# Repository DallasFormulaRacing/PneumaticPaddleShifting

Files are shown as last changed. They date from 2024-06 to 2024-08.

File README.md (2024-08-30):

# PneumaticPaddleShifting

## Table of Contents
1. [Objective](#objective)
2. [Hardware and Equipment](#hardware-and-equipment)
3. [Firmware Tech Stack](#firmware-tech-stack)
4. [Automation](#automation)
5. [Design](#design)

## Objective:
- Optimize the user's response to a down-shift and up-shift command.
- Maintain strict practices and edge cases for critical safety.
- Build the first fully-fledged DAQ with re-usable code through:
    - The Layered Architecture design pattern
    - Modularity of components
    - Hardware abstraction

## Hardware and Equipment
### Target Device
The [STM32 Nucleo F466RE](https://www.st.com/en/evaluation-tools/nucleo-f446re.html) microcontroller development board is used as the current target device for code merged to the `main` and `develop` branches. Theoretically, other Arm Cortex M4 based STM32 devices with the necessary peripherals should be able to run the same program.



## Firmware Tech Stack
- STM32 Hardware Abstraction Layer ([HAL](https://www.st.com/resource/en/user_manual/um1725-description-of-stm32f4-hal-and-lowlayer-drivers-stmicroelectronics.pdf))
  - Generated by STM32CubeMX within the CubeIDE environment, which also provides the `arm-none-eabi` toolchain.
  - Serves as a set of drivers or a Board Support Package (BSP) to interface with the microcontroller.

## Automation
- Unit tests are developed using [Google Test](https://google.github.io/googletest/) and are maintained in `Shifter_System/Tests`.
- See our [Unit Testing page](https://github.com/DallasFormulaRacing/DataAcquisition2.0/wiki/Unit-Testing) for running them locally by leveraging [Docker](https://docs.docker.com/get-started/overview/).
- Continuous Integration (CI)
  - The firmware is compiled as an stm32CubeIDE project using the following GitHub Action: [xanderhendriks/action-build-stm32cubeide](https://github.com/marketplace/actions/build-stm32cubeide-project).
  - The unit tests are compiled and ran using [CMake](https://cmake.org/cmake/help/latest/index.html) with [Ninja](https://ninja-build.org/manual.html). 

## Design

High level system diagram:

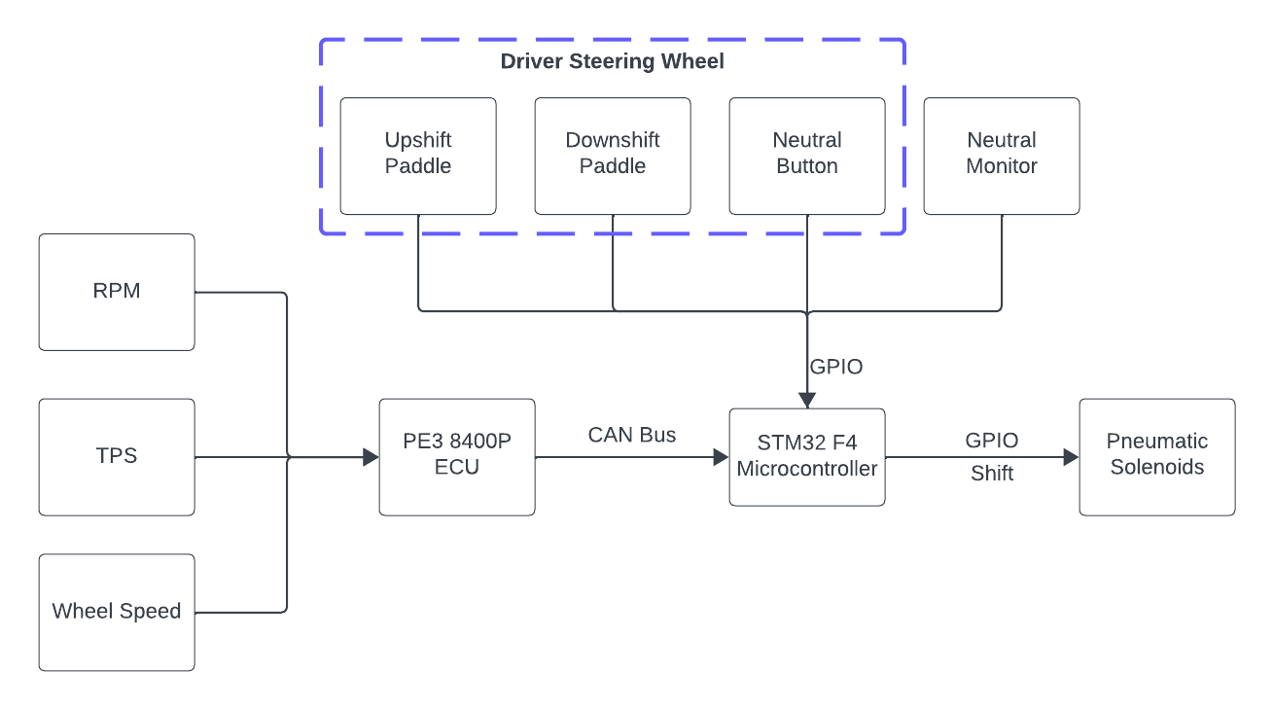
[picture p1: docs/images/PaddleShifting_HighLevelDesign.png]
High Level System Diagram


Firmware design:

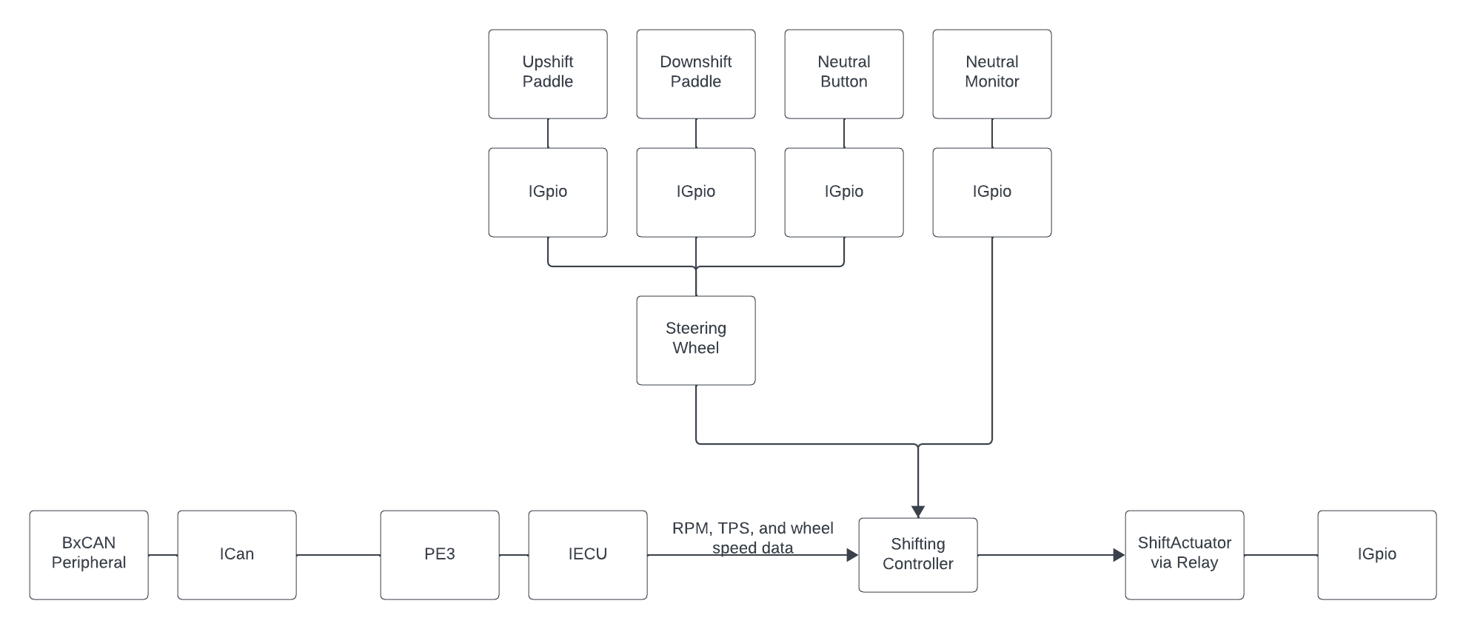
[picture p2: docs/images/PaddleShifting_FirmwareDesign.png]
Firmware Design


### User Input

It is assumed that the user inputs are simple GPIO signals (i.e., high and low voltages). The upshift and downshift paddle will request their respective shift. The neutral button is for the user to set the car into neutral, and this may be verified with a neutral “monitor”. The neutral monitor is to act as some sort of sensor or switch.  

Do note, however, that these inputs have not yet been tested. It is currently unknown whether they will require any signal “debouncing” so that the behavior is not jittery or sporadic. It has also been highly recommended to consider more fail-safe mechanisms for the scenario that the user input begins to malfunction. 

### Reading ECU Data

The device reads RPM, TPS, and wheel speeds from the PE3 8400-P ECU. This ECU implementation library was adopted from the race team’s previous efforts in other projects. 

### Shift Controller

The Shift Controller is a high-level component responsible for evaluating the driver’s shift requests. It depends on an ECU and several GPIO components to be used. Internally, a state machine is used to perform different behaviors. This approach offers the following advantages: dramatically simplifies the logic, increases performance, isolated behavior, and transition actions. The performance is increased as it only performs the conditional checks that are unique to each state. Due to the isolated behaviors, we can also easily determine and rigorously test every edge case for every state.

You may see the design of the state machine below in Figure 9. In practice, there are 6 gears. However, gears 2 through 5 had the same logic and state transition conditions, so they were condensed into a single state. So, the nomenclature was established as the following: Low Gear refers to first gear, Mid Gears refers to second to fifth gear, and High Gear refers to sixth gear. 

One important design choice is how we intended to manage the transition to/from the neutral state. In practice, to go from first to second gear, the driver typically needs to go through neutral. Although an “immediate pass-through" transition was considered, the team ultimately decided to require the driver to manually transition through neutral. This user experience will be in reminiscence of a typical vehicle to offer a more seamless and practical learning curve to use. 

It is worth mentioning that, due to time constraints in the development of the Shift Actuation, the Shift Controller is incomplete in respect to commanding for a shift. 

`ShiftController` state machine:

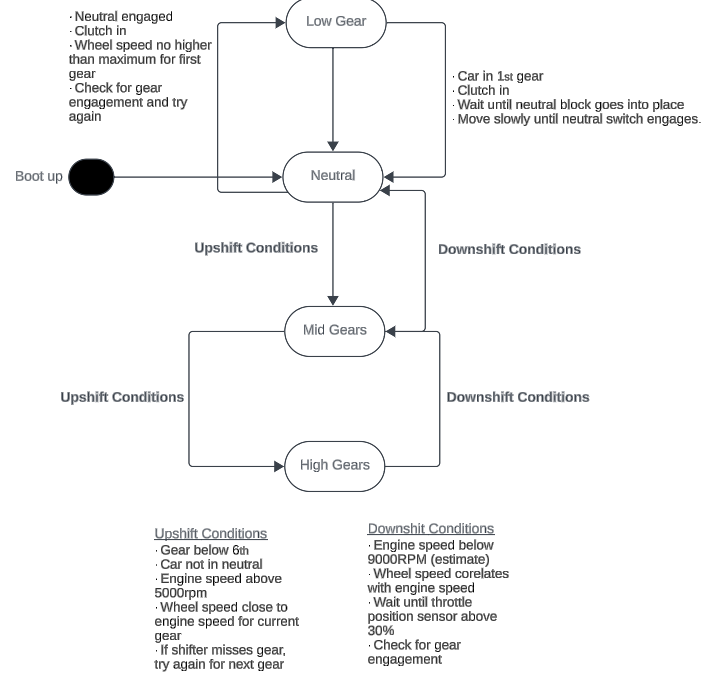
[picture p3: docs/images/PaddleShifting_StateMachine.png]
Shift Controller State Machine


### Shift Actuation

It is assumed that the required hardware interface for the shift actuator would be a GPIO (i.e., high and low) signal. However, due to time constraints, requirements of the hardware interface were not tested and verified for modifications.

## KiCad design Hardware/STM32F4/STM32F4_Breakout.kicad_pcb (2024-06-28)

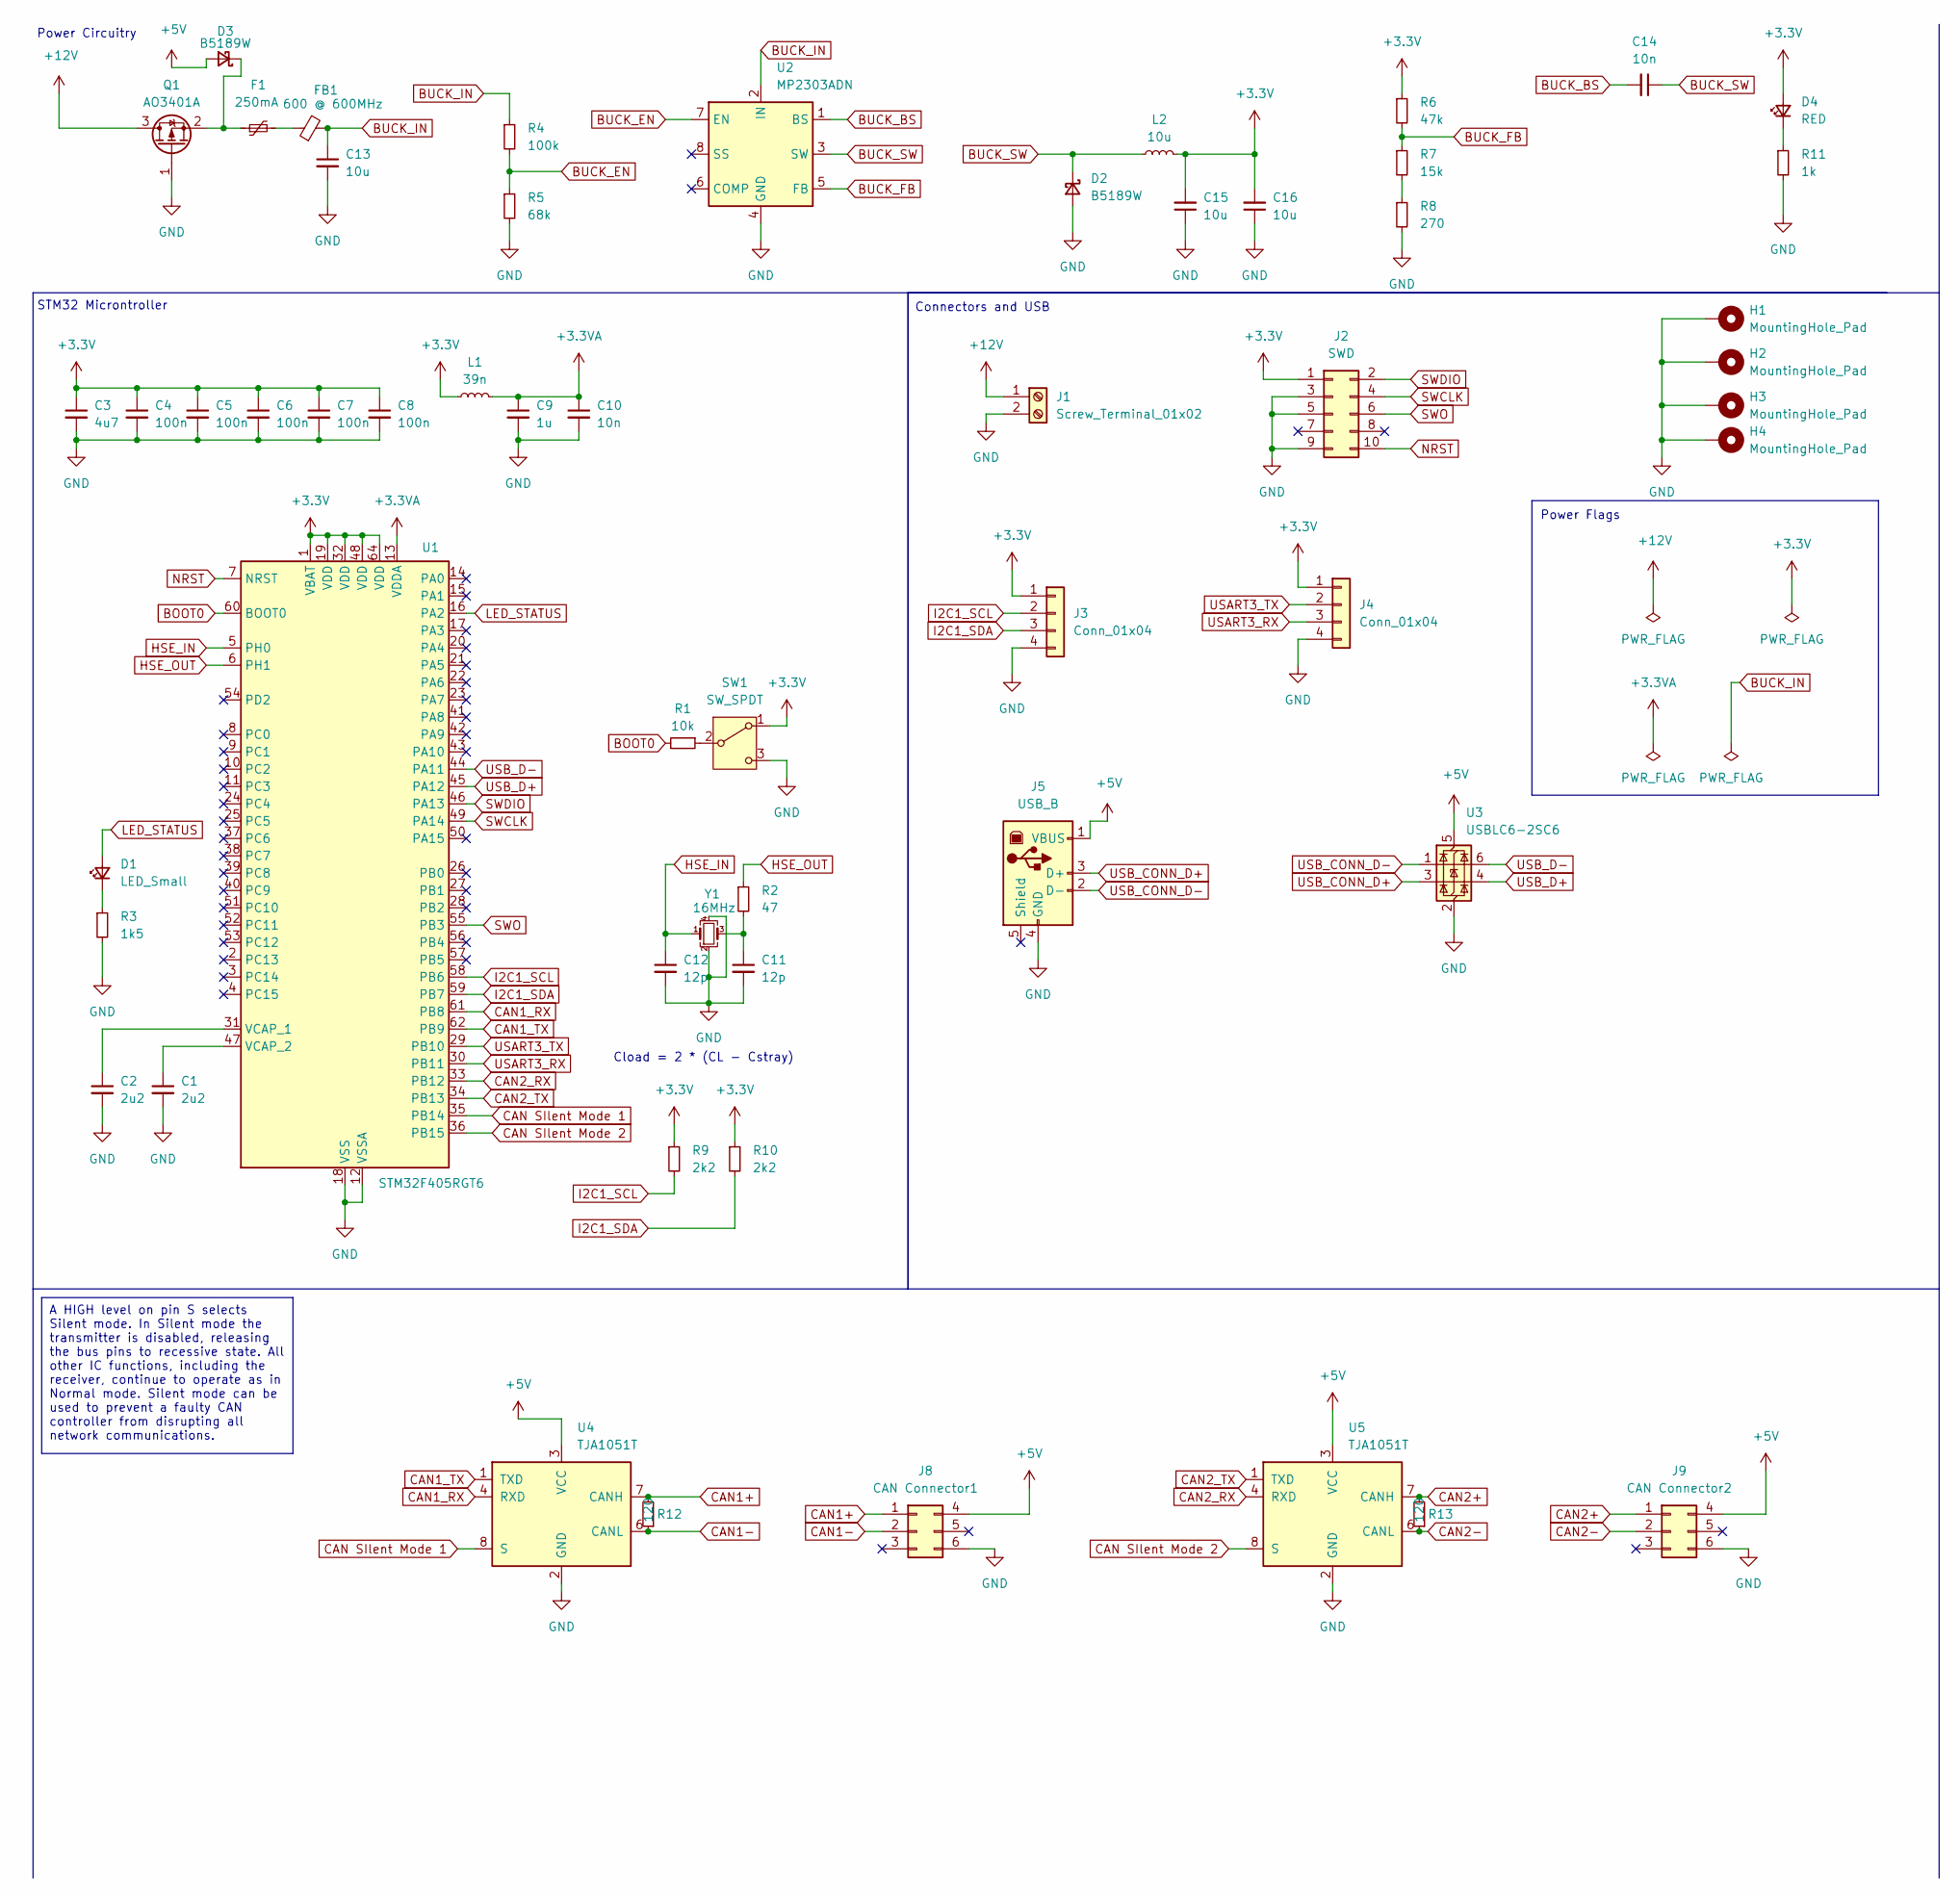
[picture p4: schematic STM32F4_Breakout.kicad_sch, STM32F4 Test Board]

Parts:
C1, C2: 2u2; C_0603_1608Metric
C3: 4u7; C_0603_1608Metric
C4, C5, C6, C7, C8: 100n; C_0402_1005Metric
C9: 1u; C_0402_1005Metric
C10: 10n; C_0402_1005Metric
C11, C12: 12p; C_0402_1005Metric
C13, C15, C16: 10u; C_1206_3216Metric
C14: 10n; C_0603_1608Metric
D1: LED_Small; LED_0603_1608Metric
D2, D3: B5189W; D_SOD-123
D4: RED; LED_0603_1608Metric
F1: 250mA; Fuse_1206_3216Metric
FB1: 600 @ 600MHz; L_0805_2012Metric
H1, H2, H3, H4: MountingHole_Pad; MountingHole_4.3mm_M4_Pad_Via
J1: Screw_Terminal_01x02; TerminalBlock_Phoenix_PT-1,5-2-3.5-H_1x02_P3.50mm_Horizontal
J2: SWD; PinHeader_2x05_P1.27mm_Vertical_SMD
J3, J4: Conn_01x04; Molex_PicoBlade_53048-0410_1x04_P1.25mm_Horizontal
J5: USB_B; USB_B_Lumberg_2411_02_Horizontal
J8: CAN Connector1; Molex_Mega-Fit_76829-0006_2x03_P5.70mm_Vertical
J9: CAN Connector2; Molex_Mega-Fit_76829-0006_2x03_P5.70mm_Vertical
L1: 39n; L_0402_1005Metric
L2: 10u; L_Sunlord_MWSA0518S
Q1: AO3401A; SOT-23
R1: 10k; R_0402_1005Metric
R2: 47; R_0402_1005Metric
R3: 1k5; R_0603_1608Metric
R4: 100k; R_0603_1608Metric
R5: 68k; R_0603_1608Metric
R6: 47k; R_0603_1608Metric
R7: 15k; R_0603_1608Metric
R8: 270; R_0603_1608Metric
R9, R10: 2k2; R_0402_1005Metric
R11: 1k; R_0603_1608Metric
R12, R13: 120; R_0603_1608Metric_Pad0.98x0.95mm_HandSolder; JLCpart# C2906988
SW1: SW_SPDT; SW_SPDT_PCM12
U1: STM32F405RGT6; LQFP-64_10x10mm_P0.5mm
U2: MP2303ADN; SOIC-8-1EP_3.9x4.9mm_P1.27mm_EP2.62x3.51mm
U3: USBLC6-2SC6; SOT-23-6
U4, U5: TJA1051T; SOIC-8_3.9x4.9mm_P1.27mm; JLCpart# C38695
Y1: 16MHz; Crystal_SMD_3225-4Pin_3.2x2.5mm

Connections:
+3.3V: C3.1, C4.1, C5.1, C6.1, C7.1, C8.1, C15.2, C16.2, D4.2 (A), J2.1, J3.1, J4.1, L1.1, L2.2, R6.1, R9.1, R10.1, SW1.1 (A), U1.1 (VBAT), U1.19 (VDD), U1.32 (VDD), U1.48 (VDD), U1.64 (VDD)
+3.3VA: C9.1, C10.1, L1.2, U1.13 (VDDA)
+5V: D3.2 (A), J5.1 (VBUS), J8.4, J9.4, U3.5 (VBUS), U4.3 (VCC), U5.3 (VCC)
+12V: J1.1, Q1.3 (D)
BOOT0: R1.2, U1.60 (BOOT0)
BUCK_BS: C14.2, U2.1 (BS)
BUCK_EN: R4.2, R5.1, U2.7 (EN)
BUCK_FB: R6.2, R7.1, U2.5 (FB)
BUCK_IN: C13.1, FB1.2, R4.1, U2.2 (IN)
BUCK_SW: C14.1, D2.1 (K), L2.1, U2.3 (SW)
CAN1+: J8.1, R12.2, U4.7 (CANH)
CAN1-: J8.2, R12.1, U4.6 (CANL)
CAN1_RX: U1.61 (PB8), U4.4 (RXD)
CAN1_TX: U1.62 (PB9), U4.1 (TXD)
CAN2+: J9.1, R13.2, U5.7 (CANH)
CAN2-: J9.2, R13.1, U5.6 (CANL)
CAN2_RX: U1.33 (PB12), U5.4 (RXD)
CAN2_TX: U1.34 (PB13), U5.1 (TXD)
CAN SIlent Mode 1: U1.35 (PB14), U4.8 (S)
CAN SIlent Mode 2: U1.36 (PB15), U5.8 (S)
GND: C1.2, C2.2, C3.2, C4.2, C5.2, C6.2, C7.2, C8.2, C9.2, C10.2, C11.2, C12.2, C13.2, C15.1, C16.1, D2.2 (A), H1.1, H2.1, H3.1, H4.1, J1.2, J2.3, J2.5, J2.9, J3.4, J4.4, J5.4 (GND), J8.6, J9.6, Q1.1 (G), R3.2, R5.2, R8.2, R11.2, SW1.3 (C), U1.12 (VSSA), U1.18 (VSS), U1.63 (VSS), U2.4 (GND), U3.2 (GND), U4.2 (GND), U5.2 (GND), Y1.2, Y1.4
HSE_IN: C12.1, U1.5 (PH0), Y1.1
HSE_OUT: R2.1, U1.6 (PH1)
I2C1_SCL: J3.2, R9.2, U1.58 (PB6)
I2C1_SDA: J3.3, R10.2, U1.59 (PB7)
LED_STATUS: D1.2 (A), U1.16 (PA2)
NRST: J2.10, U1.7 (NRST)
unnamed: C11.1, R2.2, Y1.3
unnamed: D1.1 (K), R3.1
unnamed: D3.1 (K), F1.1, Q1.2 (S)
unnamed: D4.1 (K), R11.1
unnamed: F1.2, FB1.1
unnamed: R7.2, R8.1
unnamed: R1.1, SW1.2 (B)
unnamed: C2.1, U1.31 (VCAP_1)
unnamed: C1.1, U1.47 (VCAP_2)
SWCLK: J2.4, U1.49 (PA14)
SWDIO: J2.2, U1.46 (PA13)
SWO: J2.6, U1.55 (PB3)
USART3_RX: J4.3, U1.30 (PB11)
USART3_TX: J4.2, U1.29 (PB10)
USB_CONN_D+: J5.3 (D+), U3.3 (I/O2)
USB_CONN_D-: J5.2 (D-), U3.1 (I/O1)
USB_D+: U1.45 (PA12), U3.4 (I/O2)
USB_D-: U1.44 (PA11), U3.6 (I/O1)

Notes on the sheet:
A HIGH level on pin S selects Silent mode. In Silent mode the transmitter is disabled, releasing the bus pins to recessive state. All other IC functions, including the receiver, continue to operate as in Normal mode. Silent mode can be used to prevent a faulty CAN controller from disrupting all net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
STM32 Microntroller
Power Flags
Connectors and USB
Power Circuitry
Cload = 2 * (CL - Cstray)

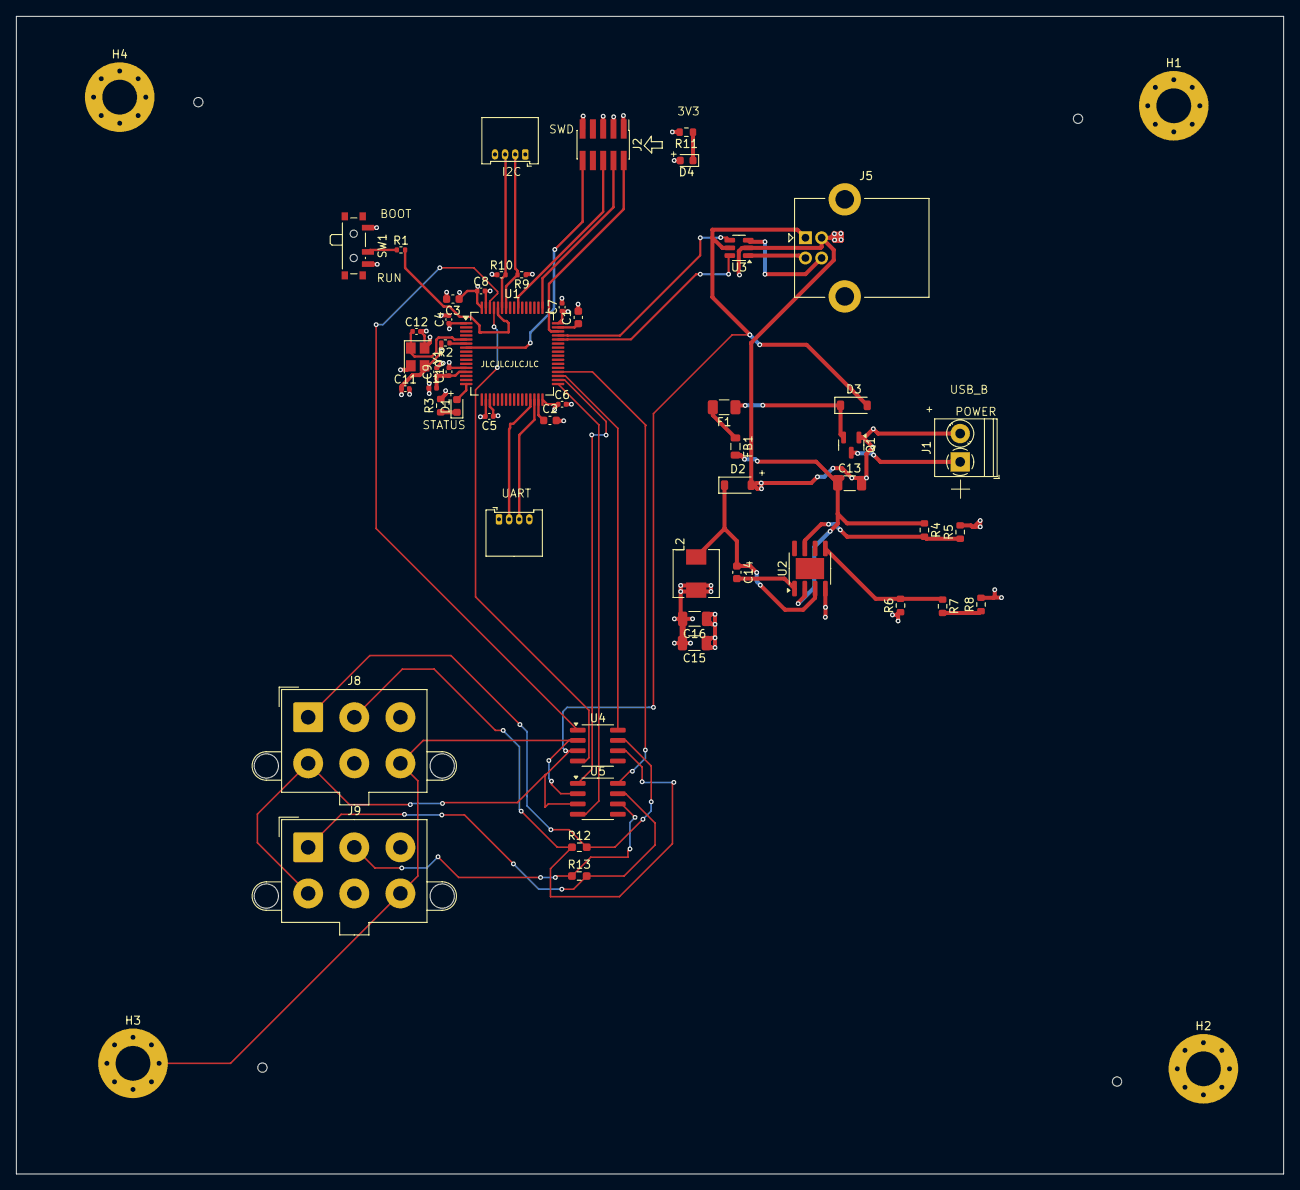
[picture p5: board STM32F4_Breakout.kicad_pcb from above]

Board: 4 copper layers, 156.6 x 143.1 mm, 56 parts (0 on the bottom side), 45 nets.

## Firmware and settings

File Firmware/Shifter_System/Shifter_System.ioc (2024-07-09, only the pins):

Mcu.UserName=STM32F446RETx
PA11.Signal=CAN1_RX
PA12.Signal=CAN1_TX
PA13.GPIO_Label=TMS
PA13.Signal=SYS_JTMS-SWDIO
PA14.GPIO_Label=TCK
PA14.Signal=SYS_JTCK-SWCLK
PA2.GPIO_Label=USART_TX
PA2.Signal=USART2_TX
PA3.GPIO_Label=USART_RX
PA3.Signal=USART2_RX
PA5.GPIO_Label=LD2 [Green Led]
PA5.Signal=GPIO_Output
PB3.GPIO_Label=SWO
PB3.Signal=SYS_JTDO-SWO
PC13.GPIO_Label=B1 [Blue PushButton]
PC13.Signal=GPXTI13
PC14-OSC32_IN.Signal=RCC_OSC32_IN
PC15-OSC32_OUT.Signal=RCC_OSC32_OUT
PH0-OSC_IN.Signal=RCC_OSC_IN
PH1-OSC_OUT.Signal=RCC_OSC_OUT

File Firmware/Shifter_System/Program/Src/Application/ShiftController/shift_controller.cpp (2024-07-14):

#include "shift_controller.hpp"

namespace application {


ShiftController::ShiftController(int16_t &rpm_observer,
								 float &tps_observer,
								 std::array<float, 2> &wheel_speeds_observer,
								 std::shared_ptr<platform::IGpio> neutral_monitor,
								 std::shared_ptr<platform::IGpio> upshift_paddle,
								 std::shared_ptr<platform::IGpio> downshift_paddle,
								 std::shared_ptr<platform::IGpio> neutral_button)
  : rpm_(rpm_observer),
	tps_(tps_observer),
	wheel_speeds_(wheel_speeds_observer),
	neutral_monitor_(neutral_monitor),
	upshift_paddle_(upshift_paddle),
	downshift_paddle_(downshift_paddle),
	neutral_button_(neutral_button) {}

ShiftController::~ShiftController() { }

void ShiftController::SetState(State* new_state) {
	if (new_state != nullptr) {
		current_state_->Exit(*this);
		current_state_ = new_state;
		current_state_->Enter(*this);
	}
}

void ShiftController::Run() {
	current_state_->Compute(*this);
}

bool ShiftController::NeutralEngaged() {
	return neutral_monitor_->Read();
}

bool ShiftController::UpshiftRequested() {
	return upshift_paddle_->ToggleDetected() &&
		   upshift_paddle_->Read();
}

bool ShiftController::UpshiftConditions() {
	// TODO: Gear below 6th
	uint8_t gear_num = 0;

	// TODO: wheel speed close to engine speed
	bool wheel_speed_close_enough = true;


	return (gear_num < 6) &&			// Gear below 6th
			!NeutralEngaged() &&				// Car not in neutral
			(rpm_ > 5000)  &&			// Engine speed above 5000
			wheel_speed_close_enough;	// Wheel speed close to engine speed for current gear
}


bool ShiftController::DownshiftRequested() {
	return downshift_paddle_->ToggleDetected() &&
		   downshift_paddle_->Read();
}

bool ShiftController::DownshiftConditions() {
	// TODO: wheel speed close to engine speed
	bool wheel_speed_close_enough = true;

	// TODO: Check for gear engagement
	bool gear_enaged = true;

	return (rpm_ < 9000) &&						// Engine speed below 9000
			wheel_speed_close_enough &&			// Wheel speed corelates with engine speed
		   (tps_ > 30.0f) &&	// Throttle posision sensor above 30%
			gear_enaged;						// Check for gear engagement 
}


//*************************************************
//					LowGear State
//*************************************************
void ShiftController::LowGear::Enter(ShiftController& context) {
	printf("[ShiftController] Entering LowGear state.\n");
}

void ShiftController::LowGear::Compute(ShiftController& context) {
	// TODO: Add the folllowing conditions (or actions?)
	//			- Wait until neutral block goes into place
	//			- Move slowly until neutral monitor engages
	if (context.DownshiftRequested()) {

		context.SetState(&context.neutral_state_);
	}


	if (context.UpshiftRequested() && context.UpshiftConditions()) {

		context.SetState(&context.mid_gear_state_);
	}
}

void ShiftController::LowGear::Exit(ShiftController& context) {
	printf("[ShiftController] Leaving LowGear state.\n");
}


//*************************************************
//					Neutral State
//*************************************************
void ShiftController::Neutral::Enter(ShiftController& context) {
	printf("[ShiftController] Entering Neutral state.\n");
}

void ShiftController::Neutral::Compute(ShiftController& context) {
	// TODO: Add the folllowing conditions
	//			- Wheel speed no higher than max for first (low) gear
	//			- Check for gear engagement and try again
	if (context.UpshiftRequested() &&
		context.NeutralEngaged()) {

		context.SetState(&context.low_gear_state_);
	}
}

void ShiftController::Neutral::Exit(ShiftController& context) {
	printf("[ShiftController] Leaving Neutral state.\n");
}


//*************************************************
//					MidGear State
//*************************************************
void ShiftController::MidGear::Enter(ShiftController& context) {
	printf("[ShiftController] Entering MidGear state.\n");
}

void ShiftController::MidGear::Compute(ShiftController& context) {

}

void ShiftController::MidGear::Exit(ShiftController& context) {
	printf("[ShiftController] Leaving MidGear state.\n");
}


//*************************************************
//					HighGear State
//*************************************************
void ShiftController::HighGear::Enter(ShiftController& context) {
	printf("[ShiftController] Entering HighGear state.\n");
}

void ShiftController::HighGear::Compute(ShiftController& context) {

}

void ShiftController::HighGear::Exit(ShiftController& context) {
	printf("[ShiftController] Leaving HighGear state.\n");
}

} // namespace application

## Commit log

2024-04-06 Create shiftCode
    Code responsible for shifting gears.
2024-04-10 Adrian's first PCB revision
    [STM32F4_Breakout.kicad_pcb, STM32F4_Breakout.kicad_sch]
2024-04-22 Consolidated Kicad projects
    [STM32F4_Breakout.kicad_pcb, STM32F4_Breakout.kicad_sch]
2024-06-14 Enabled C++. Added Blinky LED
2024-06-14 Enabled printf()
2024-06-28 CAN transceiver
    [STM32F4_Breakout.kicad_pcb, STM32F4_Breakout.kicad_sch]
2024-07-11 RPM and Wheel speed reading
2024-07-11 Integrated rpm and wheel speed into ShiftController
2024-07-11 Updated unit testing fixture to add rpm and wheel speed dependencies
    [app.cpp, shift_controller_tests.cpp]
2024-07-12 Added neutral switch gpio to ShiftController constructor
2024-07-24 Update shift_controller_tests.cpp
    Updated High gear State cases
